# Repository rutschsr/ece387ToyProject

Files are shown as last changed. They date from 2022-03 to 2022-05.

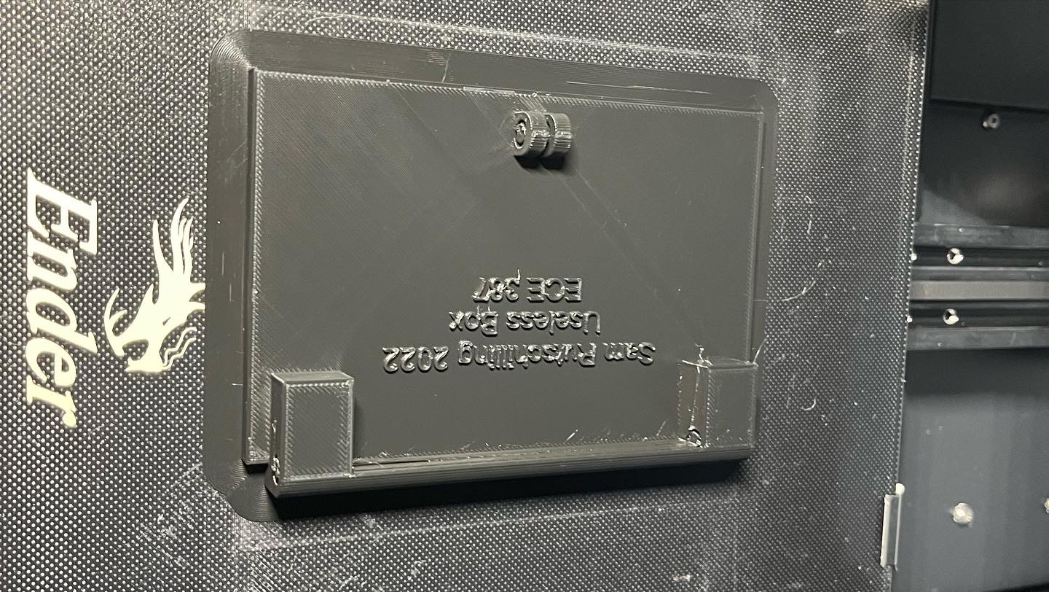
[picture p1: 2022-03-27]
Images/DoorOnPrinter.jpg

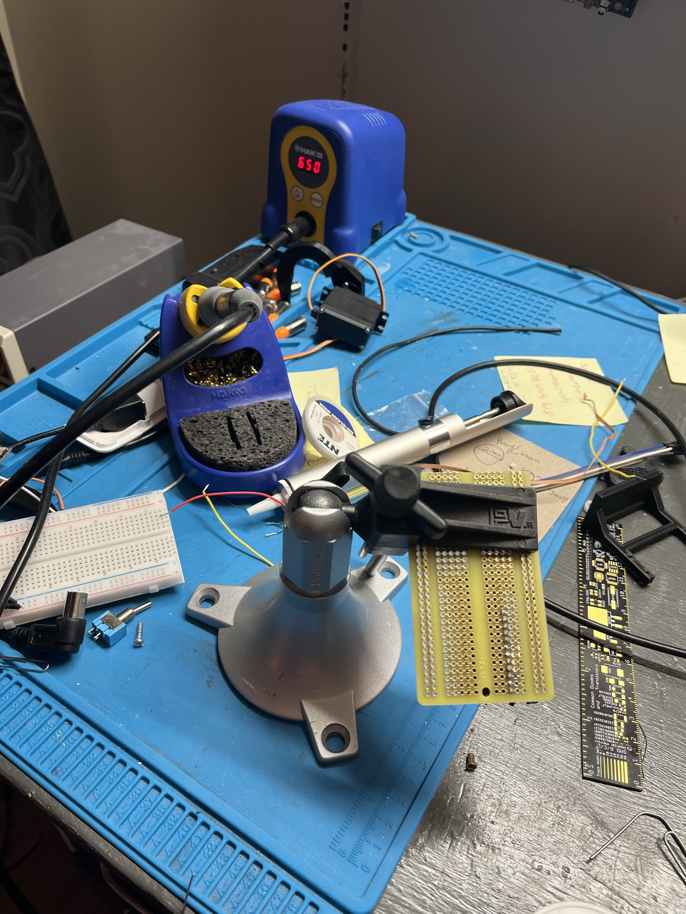
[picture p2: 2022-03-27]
Images/SolderingPerfBoard.JPEG

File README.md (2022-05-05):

# ECE 387 Individual Final Project
## Overview
This useless box is entirely 3D printed and uses a Arduino Micro (ATMEGA 32U) programmed in C using AVR-GCC and AVRDUDE. 

The operation of the Useless Box toy is very simple ... there are two switches, and when each of them are turned on, an arm emerges from inside the box and turns it back off. Therefore the Useless Box serves no real function: it is "useless".

## Operational Demonstration

Img alt text (https://www.youtube.com/watch?v=gphNHizoBe4)

## Operational Overview

The Useless box is a simple toy; it turns the switch off when it is turned on by a user. 

## 3D Printed Parts

I designed all of the mechanical parts for the Useless Box in Autodesk Fusion 360. All of the design files are located in this [Folder](https://github.com/rutschsr/ece387ToyProject/tree/main/3-D%20Parts). Each part was "sliced" (split into layers and 3D printer gcode) using [Utlimaker Cura](https://ultimaker.com/software/ultimaker-cura). I then printed each of the pieces on my Creality Ender 3 V2 3D printer using PLA (polyactic acid) filament. Each piece is is hollow and includes between 40 and 60% fill in a triangular manner to reduce print time and increase strength.

PLA Filament

### Box Bottom

Box in Fusion 360

Box in Autodesk Fusion 360. I exported the drawing to Utilimaker Cura to "slice" it before it was printed.

Box Starting to print

A raspberry pi running Octoprint is connected to my printer which provides a web interface to upload drawings and control the printer from. This printer is connected to the raspberry pi using a micro usb cable.

Complete Bottom of Box on Printer

The bottom of the box used nearly the entire print volume of the printer, took approximately 22 hours to complete, and used approximately 200g ($4-5) of material.

### Box Top

Finished Top

The top of the Useless box, still on the printer. The larger holes are where the switches are mounted, and the smaller holes are screw holes.

### Box Door

Useless box door on printer

The box with hinge mounts on the printer. The raised area on the bottom was originally planned to be a rubber band mount to close the door, but this was not necessary as the door closes by itself.

### Servo Mount

Original Small Servo Mount

The original small servo mount with a servo motor. This motor did not have enough torque and was replaced with a larger motor. The design of the Servo mount stayed the same design but was slightly larger.

### Servo Arm
Brackets and Arms Printing

The brackets and arms also took some trial and error to get correct. The larger servo motors meant that the arms had to be offset to turn off the switches, as the box was not wide enough. This was the only real design change with the arm. I used screws to attach the arm to a mount that came with the servo. This just relies on friction between the gears to stay.

## Assembly

Servo Motors inside Box

Servo Motors mounted inside The Box with switches and offset arms installed. From this view the width of the servo motors and box that required the arms to offset can be seen.

Assembled Box

Assembled box with the door open.

## Wiring and Connections
Useless Box Schematic Diagram
Above is the Schematic Diagram showing the connections for the Useless Box.

My Useless Box accepts a 5-7 V input on either the VIN jack on the outside of the box near the power switch, or the internal battery box which holds four AA batteries.

Internally, the servo motors are powered directly from the VIN port with no voltage regulation and this is why the input is limited to 7 volts. The Arduino Micro is then powered through its VIN pin. On the Arduino two digital input pins are used for the switches, and two PWM pins are used to control the servos. The wiring is very simple, with the only components being the servo motors, the switches, and bleed resistors for the switches.

Soldering perf board in progress

All of the connections are soldered or socketed to improve the reliability. I used a solder perfboard to attach all of the components and header pins for the Arduino and Servo motors.

Arduino Micro on PerfBoard

The Servo headers are on the bottom left of the perfboard, while the black 4 wire cable goes to the switches mounted on the top of the box. After I soldered the components on to the perfboard I used hotglue on all connections to ensure the wires do not break off at their connections.

## Issues

There were several issues and design changes while building the Useless Box. The first was my original choice for servo motor was very small 9g servo motors. After adding a large arm to be able to reach the switch, the motors did not have enough torque to turn the switches off. I than purchased some 20g replacement servos that are much larger and have much more torque. This required other design changes, however. Since the new motors were larger I had to redesign both the servo mounts and the servo arms. The mounts had to sit lower and be longer to fit the larger motor. The Servo arms had to have an offset so the arm would line up with a switch.

Another issue I experienced was with the Arduino. Originally I planned on using an Arduino Uno clone that I had been gifted several years ago. This has the same ATMEGA A328P on the official Arduino Uno, but as is common with the clones, does not have isolation between the USB power supply and board power supply. I found this out the hard way, by having power from my bench power supply applied through the VIN pin and USB power connected for programming. The ATMEGA microcontroller kept functioning but the USB controller failed and lost the ability to communicate. I then switched to a Arduino micro I had sitting around in preperation for a different project which fits much better inside the box but had its own challenges, such as the surface mounted micro USB programming port I managed to tear off the board almost immediately. Thankfully this was easily fixed with some solder and a few minutes of time. The real issue with the Arduino Micro came when it was time to program it in C. Those issues are explained in more detail in the C code section.

The final issue I had was following the input voltage requirements for the Servo motors. Since the servo motors are connected to the VIN connection and voltage is not regulated the voltage must stay within the servo's voltage rating of 4.0-7.2V even though the Arduino is rated for higher voltage. Unfortunately, I did not follow this and connected the Useless box to a 12V power supply I have with the same barrel jack. This did not immediately cause a failure, but one of the servos did eventually fail (and let the smoke out). I replaced the servo with a spare and it has been functioning correctly (at the correct, 5V input) since.

## Arduino Programming

The Arduino (C++) program I used for testing started with the Arduino example code for sweeping the servo motor. It is modified to move the servo motors based on the switch position. The code is located in the [Arduino Folder](https://github.com/rutschsr/ece387ToyProject/tree/main/Arduino/SimpleTest). It uses two counters in the repeating loop part of the program to sweep each of the servos up when the switch was on, and then sweep it down when it was off. This required two for loops as since the servos are sitting opposite each other, they are rotating in the opposite direction. Also included in this code was code to check that the desired position for the Servos was not exceeding what it needed to in order to turn the switches off. This is important because occassionally the arm gets stuck without turning the switch off, especially if the user is being rough with it. If this motor would get stuck it would put a large amount of stress on the mechanical compoenents and servo motors while also having other unexpected behavior. The counter would count until it overflowed, and then the desired Servo position would become very negative, which also is not desired. The Arduino code also just uses the Arduino Servo library and the Servo.write() method to write the desired location to the servo.

## C code

Although not required for this assignment I chose to challenge myself and implement the code in bare metal C code as well. I experienced two main challenges with this; programming the Arduino Micro Atmega A32U from AVRDUDE, since it operates differently then the A328P and implementing PWM on it, since the counters and registers are different then the A328P. The C code is located in the [src folder](https://github.com/rutschsr/ece387ToyProject/tree/main/src). I used the same python script as the labs to compile and program the arduino, although some modifications to the settings for AVR-GCC and avrdude had to be made to accomidate the ATMEGA A32U.

AVRDUDE and A32U

Programming the A32U from AVRDUDE initially proved to be a challenge but I was eventually able to figure out a procedure that was reliable. As with other labs, I started programming using AVRDUDE in an Ubuntu Virtual machine with the Arduino connection passed through from my Windows laptop. This was unreliable because of the procedure for programming, so eventually I decided to program the Arduino solely from a spare laptop I have that runs Ubuntu natively. 

The Arduino Micro's Atmega A32U microcontroller requires a very specific set of steps to be followed. The reset button must be pushed on the board (The Arduino IDE implements this somehow in software, but I was unable to). Then there are 8 seconds to do the remaining steps: The serial port the Arduino is attatched to must be opened at a rate of 1200bps and then immidiatley closed. I accomplished this by using the serial monitor in the Arduino IDE. Then finally the script that compiles and programs the Arduino using avr-gcc and AVRDUDE must be run. This procedure on the native linux machine had a very high success rate.

The second large issue with programming in C was implementing PWM on the A32U in the Arduino Micro. The registers and counters used for PWM on the A32U are different than those used in the Atmega A328P we used in the labs. I first tried to set up PWM the same was using the different counter configuration for the A32U but this proved time consuming and did not work. I was Thankfully able to find help [Online](https://extremeelectronics.co.in/avr-tutorials/servo-motor-control-by-using-avr-atmega32-microcontroller/) where others had implemented PWM on the Atmega A32U.

With those two issues solved, the rest of the C code is essentially ported from the Arduino Code version. The only differences are syntax and the obvious lack of the Servo.write() method. The C-Code version of the code is what is used for the demonstration video.

## Power Reduction Techniques:
As this project can be battery powered, power reduction techniques are necessary to ensure a long battery life. The useless box can be powered by 4AA batteries in a battery case that is under the useless box door. The box's ATMEGA A32U microcontroller - integrated into the Arduino Micro, is programmed using baremetal C in order to reduce the overhead and power consumption. This also uses direct manipulation of counters for PWM control so any overhead required by the Arduino libraries was eliminated. The battery life is still quite poor however, as the Servo motors can draw approximately 1 amp each under load. When operating under battery power, the AA batteries cannot output 2A for a long period of time, so battery life is poor.

## Improvements:
As with any project, by the time it was finished there were several things that I would do differently if I were to do the project again. One of these changes would be further improving the power consumption. Even with the power reduction techniques described above the power consumption and battery life are still rather poor. One easy power reduction technique I would employ if starting again is controlling the power to the servo motors using a MOSFET, so they would only have power when they are active and have a reason to be moving. Another power reduction technique I would have employed is using interrupts for the switch control, so the microcontroller could be in a ultra low power state when niether of the servos are moving. Finally instead of using the Arduino micro with the ATMEGA 32U microcontroller, I likely would use a bare ATMEGA A328P for the better packaging and power consumption.

Other power improvments for the box could include a rechargable battery system. A rechargable lithium battery could be implemented into the system power it for longer periods of time. This also could be implemented with a USB power source to easier find a power source versus the DC barrel jack on the current Useless Box. As a sidenote, the barrel jack is necessary without a permanant onboard battery due to the high power requirements of the servos that a USB power supply (especially a computer) cannot support.

Mechanical improvements I would make if I were starting again would be to design the bottom of the box with the servo mounts intergrated. This would increase the servo mounts structual integrity, would reduce their movement, and remove the need for the hot glue I added to keep the motors from moving. I also would use screws to mount the servo "arms" to the servo motors instead of relying on friction of the gears to work. While designing the initial bottom of the box I should have also considered the motion of the door opening so that I would not have had to knotch the door on the sides to let it open. This was the first project I had completed with 3-D printed parts and Fusion 360, so it was a learning expierence both with the 3-D design software and my 3-D printer.

## Cost

Cost breakdown. Costs for 3D printed parts are estimated from the slicer's estimate of the filament required for printing.

| Part | Quantity | Cost | Note |
| --- | --- | --- | --- |
| Box Bottom | 1 | $5.74 | PLA |
| Box Top | 1 | $1.10 | PLA |
| Box Door | 1 | $1.02 | PLA |
| Servo Arms | 2 | $0.55 | PLA |
| Servo Mounts | 2 | $0.55 | PLA |
| Original Servos| 2 | $10.99 |  |
| Larger Servos| 2 | $22.35 |  |
| Switches | 2 | $1.60 |  |
| Arduino Micro | 1 | $21.00 |  |
| Perfboard | 1 | $6.99 | Adafruit |
| Hinge Rod | 1 | $8.51 |  |
| Miscelaneous | N/A | $5 | Other Various Parts |

Total: $85.40

## More Information:

Additional Documentation found at: https://srutschilling.net/ECE387/ToyProject/

(Site will be undergoing maintenance between May 15-June 1 2022)

Additional help with PWM on ATMEGA 32U from: https://extremeelectronics.co.in/avr-tutorials/servo-motor-control-by-using-avr-atmega32-microcontroller/

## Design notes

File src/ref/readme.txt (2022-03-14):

Sam Rutschilling
Lab 3: 
ECE 387 Spring 2022
Miami University

Febuary 10,2022

Youtube Demonstration of working project:
https://youtu.be/_FFq0tg9W6I

The Arduino was programmed using modified compile_script on Linux Virtual Machine (slight changes
to change \ to / and remove .exe in avrdude. The script will likely not work completley correctly for Windows machines.

The Com port passed to my Linux Virtual Machine by VMWARE Workstation is defined as /dev/ttyACM0, this is used for programming.
This was also used using the USART library for serial communication while trying to debug.

running the command "python compile_script.py 4" compiles the program and uploads it to the arduino using /dev/ttyACM0.

Additional files and compiled files can be removed then using the command "python compile_script.py 0" This is equivalent to "clean" in Visual Studio.

Also added to the program were Design by contract Pre and Post proccessor functions. The preprocessor functions for the stoplight function were tested in a video linked below.
For this video one of the function calls explicitly calls for two of the lights to be on, this causes the pin 13 led to light up and the program to be in a DBC error state. This
DBC pre function uses Exculsive OR call. PRE and POST DBC functions turn on PIN13 (the built in Arduino LED) if they fail. This tells the user/programmer that an error occured. POST_ errors turn
the LED on for half of the time that PRE_ issues do so that differentiates which function failed. This is helpful for debugging. The compiled program will be smaller and will execute faster without DBC functions
Included. Since they are handled using preprocessor directives it should make no difference to fully remove them as the preprocessor and compiler will ignore them and not compile them if they are turned off. Similarly,
in C++ I have used #If 0 preprocessor directives to turn off complete blocks of code, since they are turned off by preprocessor directives they will be ignored at the preprocessing stage and not handled by the compiler.

Link of DBC Error Video:
https://youtu.be/MKCNsZm0w2o

A Pull down resistor (large value 4K+ Ohm) is necessary for an input button on the arduino. This keeps the input pin grounded and from "floating" if the button is not pushed and the value is not high. This will keep
unexpected results from occuring where the arduino reads the input as high when the button was not pushed.

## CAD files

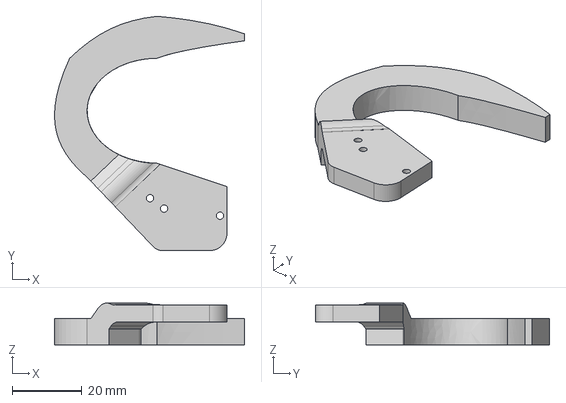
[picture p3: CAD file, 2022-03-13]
3-D Parts/STEP/UselessBoxArmOffset v3.step
54.3 x 67.0 x 12.0 mm

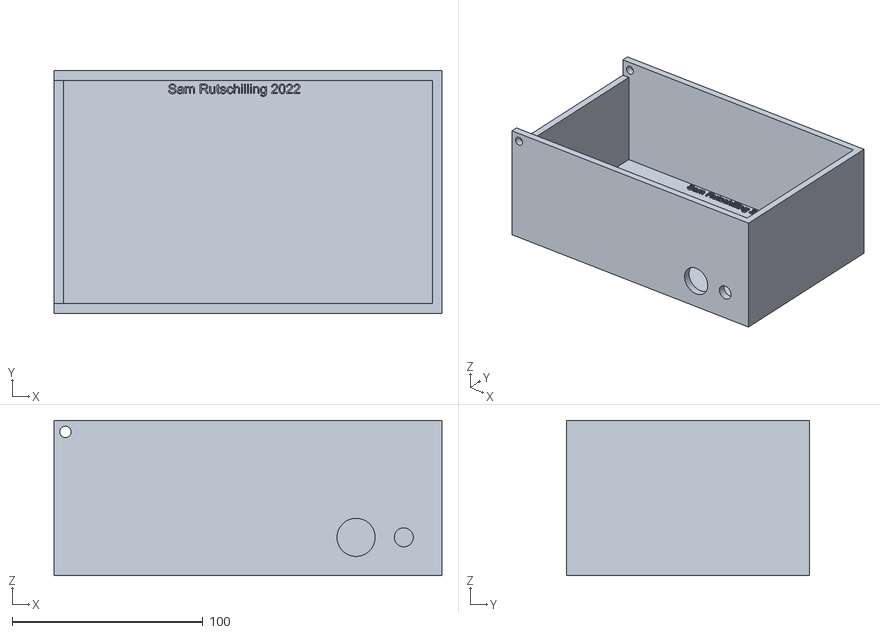
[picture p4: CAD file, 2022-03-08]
3-D Parts/STL/UselessBoxBottom v3.stl
203.2 x 127.0 x 81.2

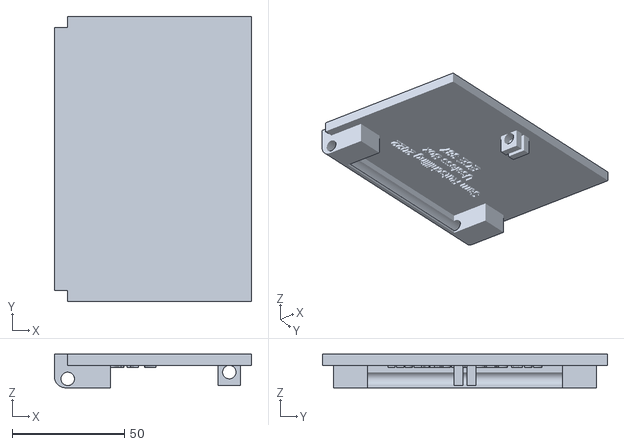
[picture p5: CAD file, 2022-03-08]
3-D Parts/STL/UselessBoxDoor v3.stl
88.0 x 127.0 x 15.0

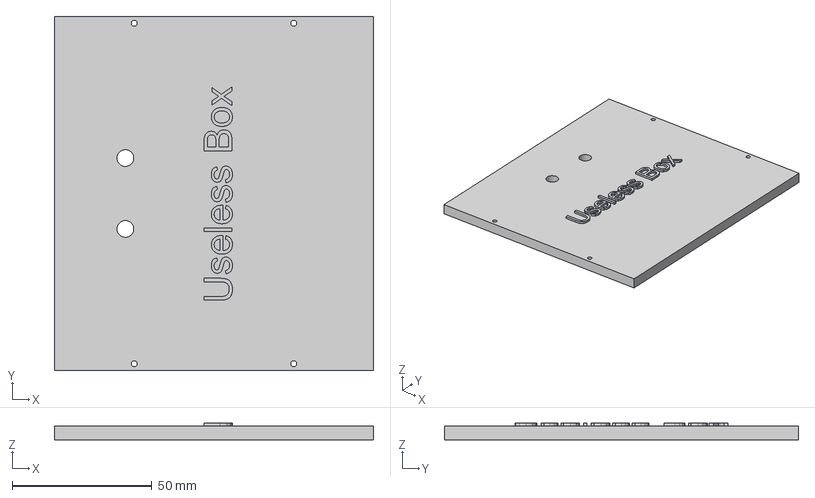
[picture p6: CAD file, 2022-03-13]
3-D Parts/STEP/UselessBoxTop v6.step
114.3 x 127.0 x 6.00 mm

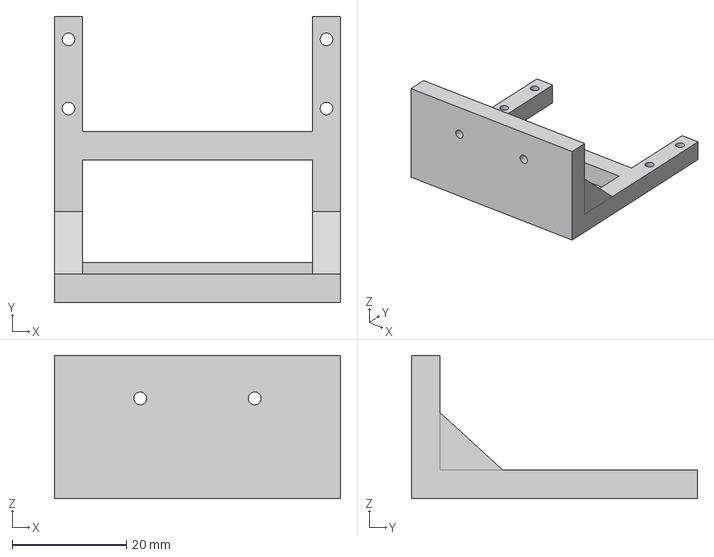
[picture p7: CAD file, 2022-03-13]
3-D Parts/STEP/UselessBoxServoMountBiggerServo v1.step
50.0 x 50.0 x 25.0 mm

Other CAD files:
3-D Parts/STEP/UselessBoxBottom v4.step
3-D Parts/STL/UselessBoxTop v5.stl
3-D Parts/STEP/UselessBoxArmOffsetReflect v2.step
3-D Parts/STEP/UselessBoxDoor v4.step
3-D Parts/Fusion 360/UselessBoxArmOffset v3.f3d
3-D Parts/Fusion 360/UselessBoxArmOffsetReflect v2.f3d
3-D Parts/Fusion 360/UselessBoxBottom v3.f3d
3-D Parts/Fusion 360/UselessBoxDoor v4.f3d
3-D Parts/Fusion 360/UselessBoxServoMountBiggerServo v1.f3d
3-D Parts/Fusion 360/UselessBoxTop v6.f3d

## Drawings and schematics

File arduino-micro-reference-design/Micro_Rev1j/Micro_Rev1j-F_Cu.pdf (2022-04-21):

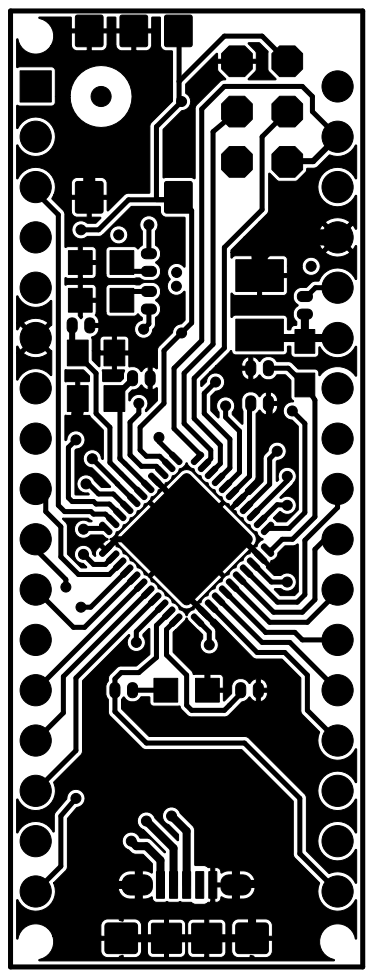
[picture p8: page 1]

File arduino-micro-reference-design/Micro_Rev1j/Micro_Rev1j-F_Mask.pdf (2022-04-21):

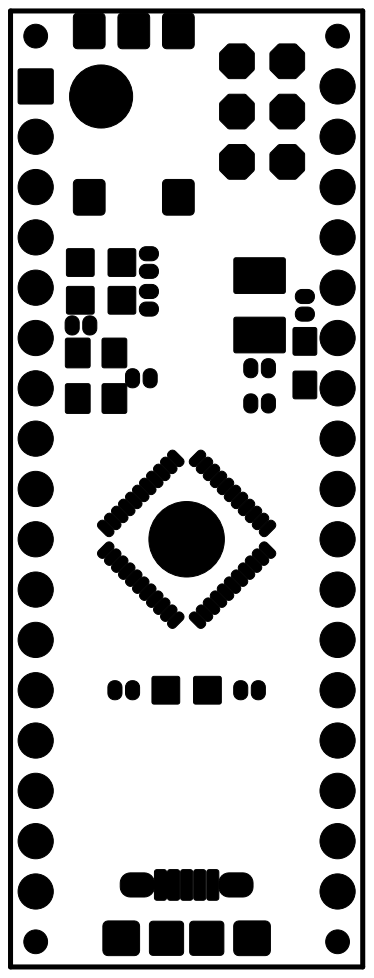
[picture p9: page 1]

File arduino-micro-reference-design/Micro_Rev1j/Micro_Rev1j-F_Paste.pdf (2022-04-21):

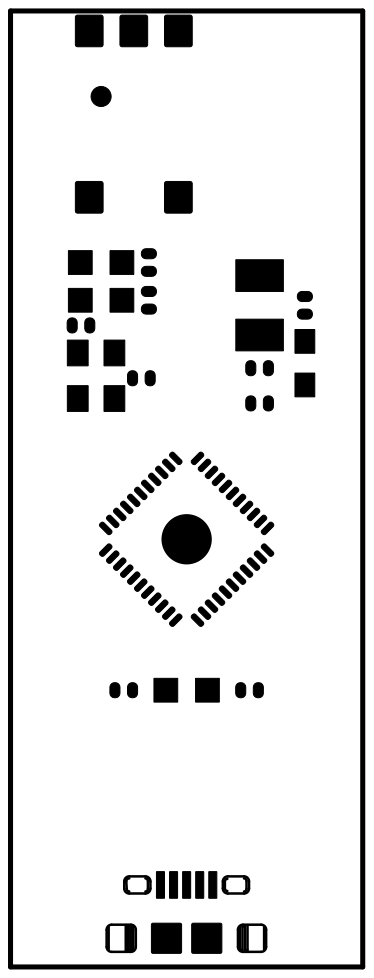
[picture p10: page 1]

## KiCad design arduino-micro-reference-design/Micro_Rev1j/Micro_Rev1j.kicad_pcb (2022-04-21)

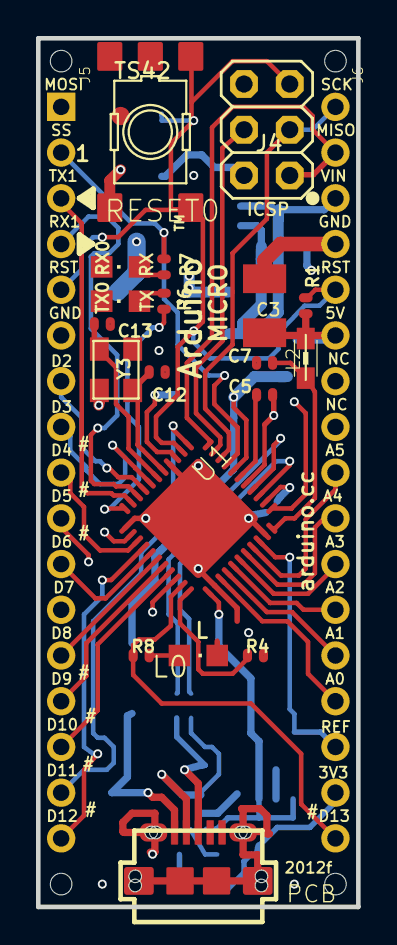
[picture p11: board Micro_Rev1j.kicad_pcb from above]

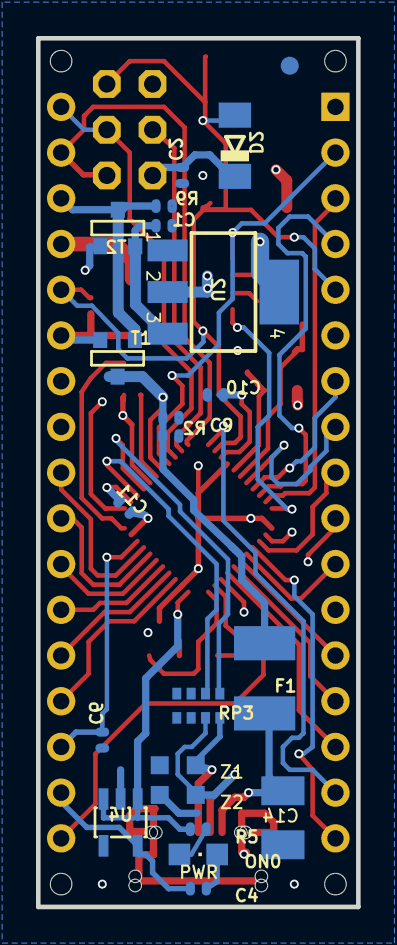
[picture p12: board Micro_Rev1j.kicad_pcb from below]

Board: 4 copper layers, 17.8 x 48.3 mm, 49 parts (22 on the bottom side), 47 nets.

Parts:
@HOLE0, @HOLE1, @HOLE2, @HOLE3: (no value)
C1, C2, C6, C9, C10, C11: 100n; C0402
C3, C14: 22u; SMC_B
C4, C5, C7: 1uF; C0402
C12, C13: 22pF; C0402
D2: CD1206-S01575; MINIMELF
F1: MF-MSMF050-2 500mA; L1812
FRAME1: DNP; FRAME
J3: USB-MICRO!!!; CON2_USB_MICRO_B_AT
J4: 3x2M; 2X03
J5: HEAD17-NOSS
J6: HEAD17-NOSS-1
L0: green; CHIPLED_0805
L2: MH2029-300Y; 0805
ON0: blue; CHIPLED_0805
R1, R2, R4, R9: 10K; R0402
R5, R6, R7, R8: 1K; R0402
RESET0: TS42
RP3: 22R; CAY16
RX0: yellow; CHIPLED_0805
T1: FDN340P/PMV48XP; SOT-23
T2: PMV48XP; SOT-23
TX0: yellow; CHIPLED_0805
U1: ATMEGA32U4-XUMU; QFN44ML7X7
U2: NCP1117-5; SOT223
U4: LP2985-33DBVR; SOT23-DBV
U$37: FIDUCIALMOUNT; FIDUCIA-MOUNT
U$53: FIDUCIAL1X2; FIDUCIAL-1X2
Y3: 16MHz KX-7; CRYSTAL-3.2-2.5
Z1, Z2: CG0603MLC-05E; CT_CN0603

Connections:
3V3: C4.1, J6.16, U4.5
+5V: C2.1, C3.+, C10.1, C11.1, D2.C, J4.2, J6.6, L2.1, R1.1, R5.1, T1.2, T2.3, U1.2, U1.14, U1.24, U1.34, U2.2, U2.4, U4.1, U4.3
+VIN: C1.1, T2.2, U2.3
A0: J6.14, U1.36
A1: J6.13, U1.37
A2: J6.12, U1.38
A3: J6.11, U1.39
A4: J6.10, U1.40
A5: J6.9, U1.41
AREF: C6.1, J6.15, U1.42
AVCC: C7.1, L2.2, U1.44
D0/RX: J5.4, U1.20
D1/TX: J5.3, U1.21
D2/SDA: J5.7, U1.19
D3/SCL: J5.8, U1.18
D4*: J5.9, U1.25
D5*: J5.10, U1.31
D6*: J5.11, U1.27
D7: J5.12, U1.1
D+: J3.P3, RP3.8, Z1.1
D-: J3.P2, RP3.7, Z2.1
GND: C1.2, C2.2, C3.-, C4.2, C5.2, C6.2, C7.2, C9.2, C10.2, C11.2, C12.1, C13.1, C14.-, J3.P5, J3.S1, J3.S2, J3.S3, J3.S4, J3.S5, J3.S6, J4.6, J5.6, J6.4, L0.C, ON0.C, R2.1, R4.2, R9.1, RESET0.3, RESET0.4, RESET0.5, RP3.3, RP3.4, RP3.5, RP3.6, RX0.C, TX0.C, U1.5, U1.15, U1.23, U1.35, U1.43, U1.EXP, U2.1, U4.2, Y3.2, Y3.4, Z1.2, Z2.2
HWB: R4.1, U1.33
IO8: J5.13, U1.28
IO9*: J5.14, U1.29
IO10*: J5.15, U1.30
IO11*: J5.16, U1.12
IO12*: J5.17, U1.26
IO13*: J6.17, R8.1, U1.32
MISO: J4.1, J6.2, U1.11
MOSI: J4.4, J5.1, U1.10
unnamed: R7.2, RX0.A
unnamed: ON0.A, R5.2
unnamed: R6.2, TX0.A
unnamed: L0.A, R8.2
RD+: RP3.1, U1.4
RD-: RP3.2, U1.3
RESET: D2.A, J4.5, J5.5, J6.5, R1.2, RESET0.1, RESET0.2, U1.13
RXLED/SS: J5.2, R7.1, U1.8
SCK: J4.3, J6.1, U1.9
TXLED: R6.1, U1.22
UCAP: C5.1, U1.6
VIN: J6.3, R9.2, T1.3, T2.1
VUSB: C9.1, F1.2, R2.2, T1.1, U1.7
VUSBD: C14.+, F1.1, J3.P1
XTAL1: C13.2, U1.17, Y3.3
XTAL2: C12.2, U1.16, Y3.1

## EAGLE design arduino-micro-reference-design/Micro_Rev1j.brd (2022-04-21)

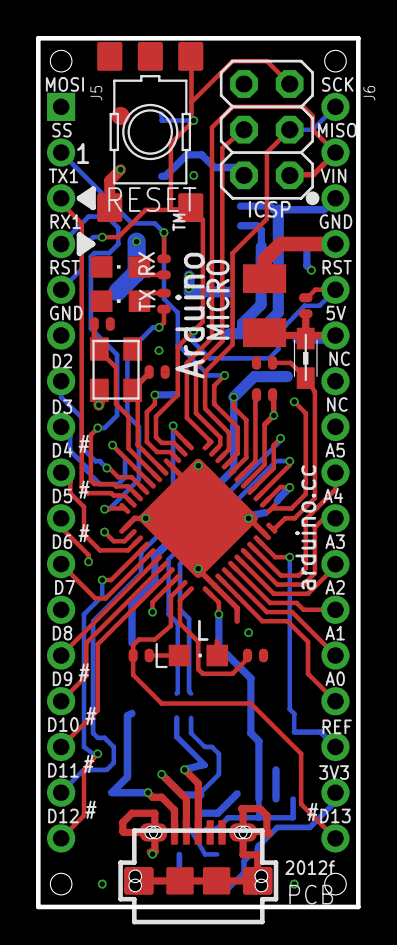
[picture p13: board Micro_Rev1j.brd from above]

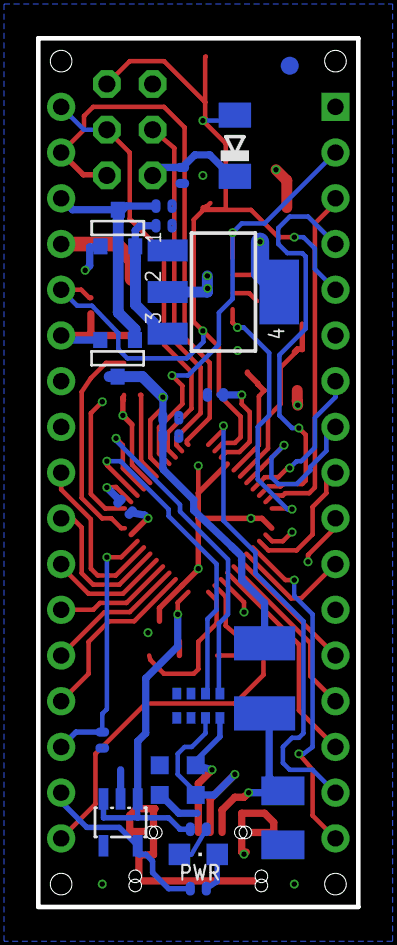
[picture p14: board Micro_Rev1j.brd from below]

Board: 4 copper layers, 17.8 x 48.3 mm, 45 parts (22 on the bottom side), 47 nets.

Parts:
C1, C2, C6, C9, C10, C11: 100n; C0402
C3, C14: 22u; SMC_B
C4, C5, C7: 1uF; C0402
C12, C13: 22pF; C0402
D2: CD1206-S01575; MINIMELF
F1: MF-MSMF050-2 500mA; L1812
FRAME1: DNP; FRAME
J3: USB-MICRO!!!; CON2_USB_MICRO_B_AT
J4: 3x2M; 2X03
J5: HEAD17-NOSS
J6: HEAD17-NOSS-1
L: green; CHIPLED_0805
L2: MH2029-300Y; 0805
ON: blue; CHIPLED_0805
R1, R2, R4, R9: 10K; R0402
R5, R6, R7, R8: 1K; R0402
RESET: TS42
RP3: 22R; CAY16
RX: yellow; CHIPLED_0805
T1: FDN340P/PMV48XP; SOT-23
T2: PMV48XP; SOT-23
TX: yellow; CHIPLED_0805
U1: ATMEGA32U4-XUMU; QFN44ML7X7
U2: NCP1117-5; SOT223
U4: LP2985-33DBVR; SOT23-DBV
U$37: FIDUCIALMOUNT; FIDUCIA-MOUNT
U$53: FIDUCIAL1X2; FIDUCIAL-1X2
Y3: 16MHz KX-7; CRYSTAL-3.2-2.5
Z1, Z2: CG0603MLC-05E; CT/CN0603

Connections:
3V3: C4.1, J6.16, U4.5
+5V: C2.1, C3.+, C10.1, C11.1, D2.C, J4.2, J6.6, L2.1, R1.1, R5.1, T1.2, T2.3, U1.2, U1.14, U1.24, U1.34, U2.2, U2.4, U4.1, U4.3
+VIN: C1.1, T2.2, U2.3
A0: J6.14, U1.36
A1: J6.13, U1.37
A2: J6.12, U1.38
A3: J6.11, U1.39
A4: J6.10, U1.40
A5: J6.9, U1.41
AREF: C6.1, J6.15, U1.42
AVCC: C7.1, L2.2, U1.44
D0/RX: J5.4, U1.20
D1/TX: J5.3, U1.21
D2/SDA: J5.7, U1.19
D3/SCL: J5.8, U1.18
D4*: J5.9, U1.25
D5*: J5.10, U1.31
D6*: J5.11, U1.27
D7: J5.12, U1.1
D+: J3.P3, RP3.8, Z1.1
D-: J3.P2, RP3.7, Z2.1
GND: C1.2, C2.2, C3.-, C4.2, C5.2, C6.2, C7.2, C9.2, C10.2, C11.2, C12.1, C13.1, C14.-, J3.P5, J3.S1, J3.S2, J3.S3, J3.S4, J3.S5, J3.S6, J4.6, J5.6, J6.4, L.C, ON.C, R2.1, R4.2, R9.1, RESET.3, RESET.4, RESET.5, RP3.3, RP3.4, RP3.5, RP3.6, RX.C, TX.C, U1.5, U1.15, U1.23, U1.35, U1.43, U1.EXP, U2.1, U4.2, Y3.2, Y3.4, Z1.2, Z2.2
HWB: R4.1, U1.33
IO8: J5.13, U1.28
IO9*: J5.14, U1.29
IO10*: J5.15, U1.30
IO11*: J5.16, U1.12
IO12*: J5.17, U1.26
IO13*: J6.17, R8.1, U1.32
MISO: J4.1, J6.2, U1.11
MOSI: J4.4, J5.1, U1.10
unnamed: R7.2, RX.A
unnamed: ON.A, R5.2
unnamed: R6.2, TX.A
unnamed: L.A, R8.2
RD+: RP3.1, U1.4
RD-: RP3.2, U1.3
RESET: D2.A, J4.5, J5.5, J6.5, R1.2, RESET.1, RESET.2, U1.13
RXLED/SS: J5.2, R7.1, U1.8
SCK: J4.3, J6.1, U1.9
TXLED: R6.1, U1.22
UCAP: C5.1, U1.6
VIN: J6.3, R9.2, T1.3, T2.1
VUSB: C9.1, F1.2, R2.2, T1.1, U1.7
VUSBD: C14.+, F1.1, J3.P1
XTAL1: C13.2, U1.17, Y3.3
XTAL2: C12.2, U1.16, Y3.1

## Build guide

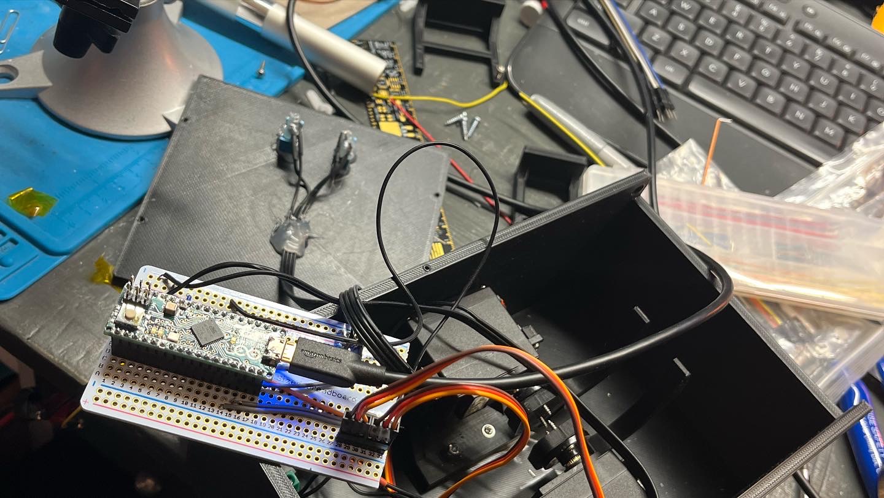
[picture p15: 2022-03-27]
Images/WiringConnected.jpg

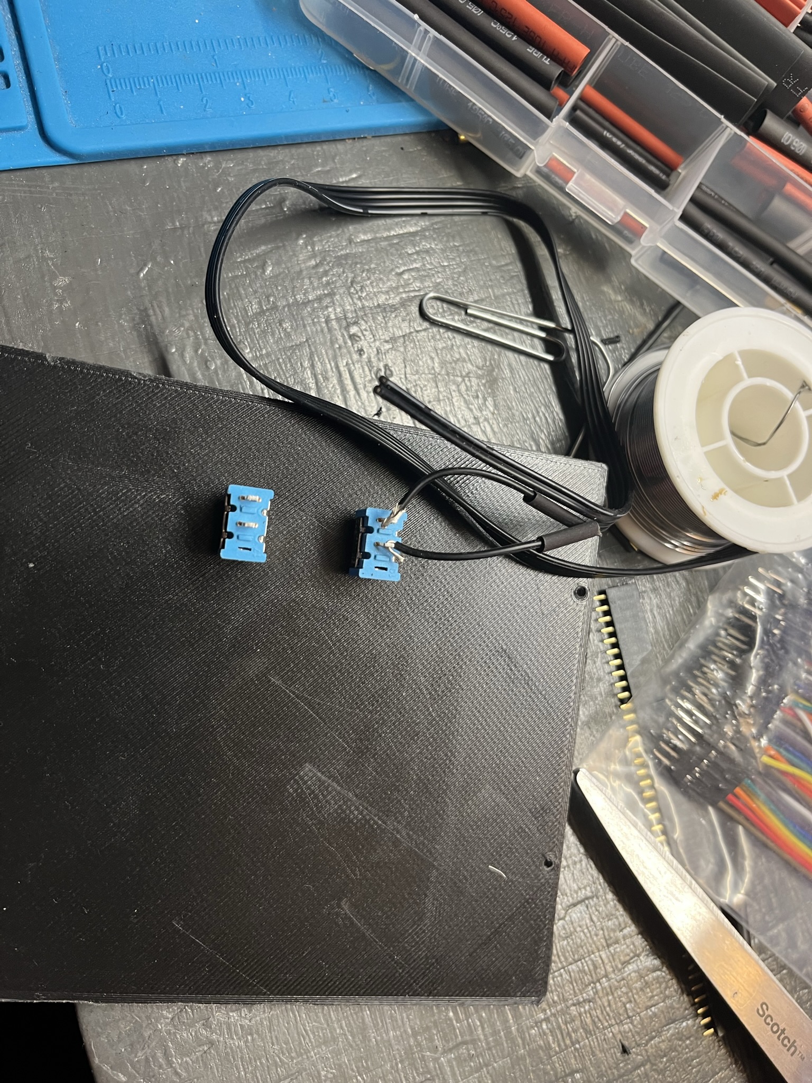
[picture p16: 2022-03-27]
Images/SolderingSwitches.JPEG

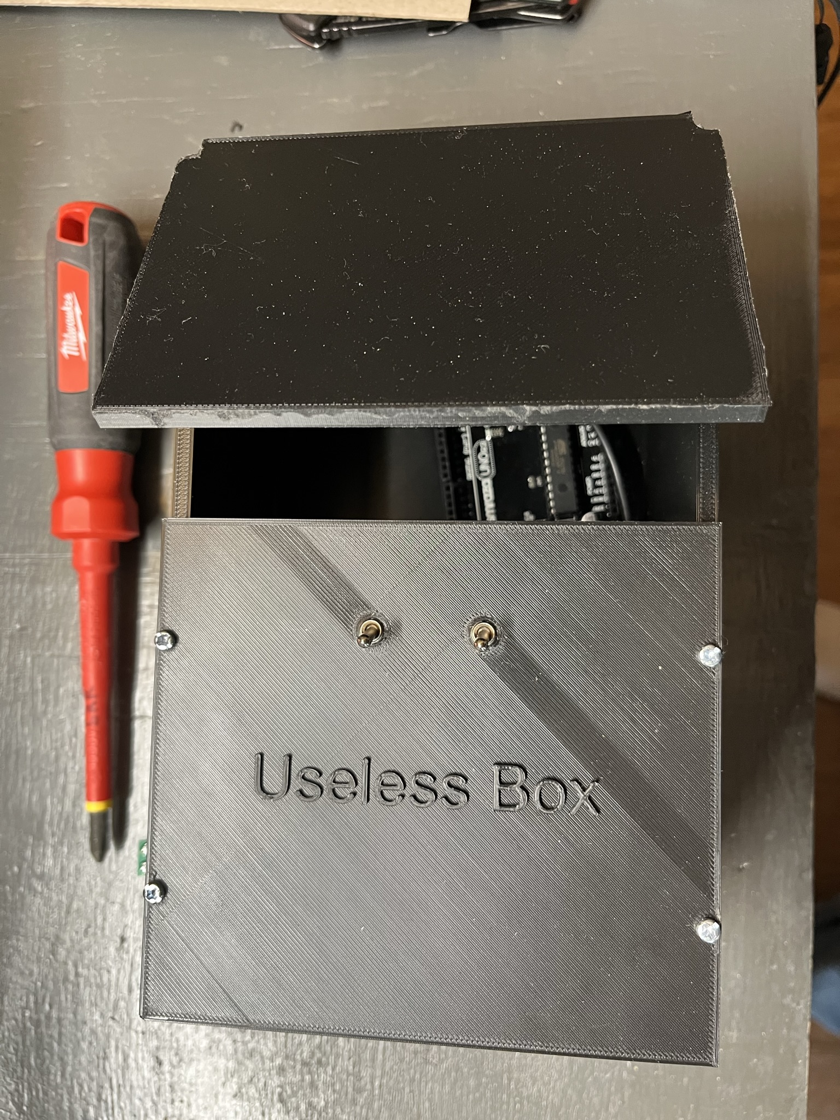
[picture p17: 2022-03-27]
Images/AssembledBox1.JPEG

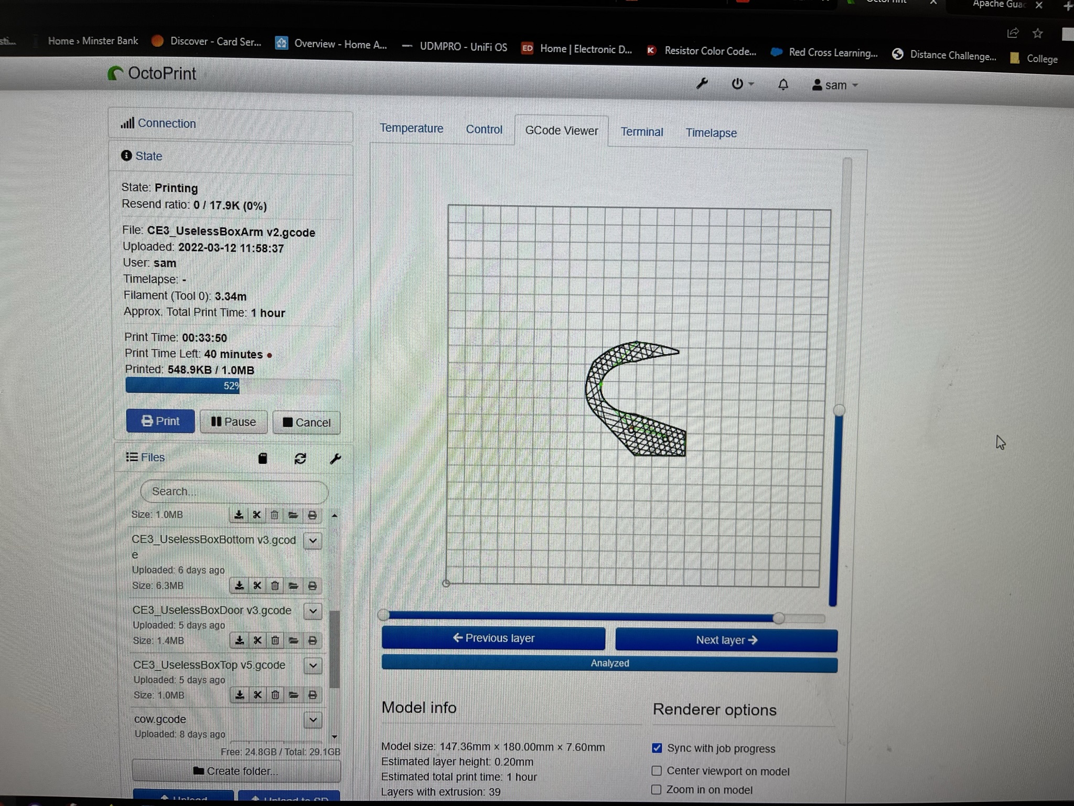
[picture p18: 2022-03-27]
Images/ArmInOctoPrint.JPEG

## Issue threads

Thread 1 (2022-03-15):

Create C code

rutschsr, 2022-03-15:
Create C code with notes in Arduino code. Should use hardware PWM as in stoplight lab. Inputs do not need debouncing as they are switches not buttons.

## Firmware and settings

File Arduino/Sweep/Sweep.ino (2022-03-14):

/* Sweep
 by BARRAGAN <http://barraganstudio.com>
 This example code is in the public domain.

 modified 8 Nov 2013
 by Scott Fitzgerald
 http://www.arduino.cc/en/Tutorial/Sweep
*/

#include <Servo.h>

Servo myservo;  // create servo object to control a servo
// twelve servo objects can be created on most boards
Servo Servo2;

int pos = 0;    // variable to store the servo position

void setup() {
  myservo.attach(9);
  Servo2.attach(10);// attaches the servo on pin 9 to the servo object
}

void loop() {
  for (pos = 50; pos <= 138; pos += 1) { // goes from 0 degrees to 180 degrees
    // in steps of 1 degree
    myservo.write(pos);
    Servo2.write(175-pos); // tell servo to go to position in variable 'pos'
    delay(5);                       // waits 15ms for the servo to reach the position
  }
    myservo.write(138);
    Servo2.write(175-138);// tell servo to go to position in variable 'pos'
    delay(1000); 
  
  for (pos = 138; pos >= 50; pos -= 1) { // goes from 180 degrees to 0 degrees
    myservo.write(pos);
    Servo2.write(175-pos);              // tell servo to go to position in variable 'pos'
    delay(5);                       // waits 15ms for the servo to reach the position
  }
  myservo.write(50);
  Servo2.write(175-50);
  // tell servo to go to position in variable 'pos'
    delay(5000); 
}

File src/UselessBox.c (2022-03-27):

#include <avr/io.h>
#include <util/delay.h>

//PWM on Atmega32u using help from:
//https://extremeelectronics.co.in/avr-tutorials/servo-motor-control-by-using-avr-atmega32-microcontroller/

// Switch 1 on 6 (PD7)
// Switch 2 on 7 (PE6)
#define button1 PD7
#define button2 PE6

// Servo 1 on 9 (PB5)
// Servo 2 on 10 (PB6)

// Forward Declerations
void pwm_hw_setup();
void pwm(int servo1, int servo2);

int button1state = 1;
int button2state = 1;
int servo1pos = 85;
int servo2pos = 125;

int main()
{
     pwm_hw_setup();

    DDRC |= _BV(DDC7);

    while (1)
    {
        button1state = (PIND & (1 << button1));
        button2state = (PINE & (1 << button2));

       if(button1state==0){
           if(servo1pos<200){
               servo1pos++;
           }
       }
       else{
           if(servo1pos>=85){
               servo1pos--;
           }
       }
       
       
       
        if (button2state==0)
        {
            PORTC |= _BV(PORTC7);
            if(servo2pos>60){
                servo2pos--;
            }
        }
        else
        {
            if(servo2pos<=185){
                servo2pos++;
            }
            PORTC &= ~_BV(PORTC7);
        }
        pwm(servo1pos ,servo2pos);
        _delay_ms(2);
    }
}

void pwm_hw_setup()
{
	TCCR1A|=(1<<COM1A1)|(1<<COM1B1)|(1<<WGM11);        //NON Inverted PWM
   TCCR1B|=(1<<WGM13)|(1<<WGM12)|(1<<CS11)|(1<<CS10); //PRESCALER=64 MODE 14(FAST PWM)

   ICR1=4999;  //fPWM=50Hz (Period = 20ms Standard).

   DDRB|=(1<<PB5)|(1<<PB6);   //PWM Pins as Out
}


void pwm(int servo1, int servo2)
{
	servo1=servo1*2+100;
    servo2=servo2*2+100;

	
      OCR1A=servo1;  //90 degree
      OCR1B=servo2;  //90 degree



	
	
		/* IF - button1 is pressed - increase the PWM duty cycle by 12.5% or 1/8 */
		// PIN 10 - yellow
		//OCR1A=(float)servo1/(float)180*step16;
		// PIN 11 - green
		//OCR1B =(float)servo2/(float)180*step16;
		// PIN 3 - red
		//OCR2B += step8;
	
}

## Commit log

2022-03-08 Add STL
    add STL files for some of the 3D printed parts
    [UselessBoxBottom v3.stl, UselessBoxDoor v3.stl, UselessBoxTop v5.stl]
2022-03-13 Add Remaining 3-D print files
    [UselessBoxArmOffset v3.f3d, UselessBoxArmOffset v3.step, UselessBoxArmOffsetReflect v2.f3d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]
2022-03-15 Update SimpleTest.ino
    Add some new behavior to fix errors with counters running too high
    [SimpleTest.ino]
2022-03-27 Switch Test
2022-03-27 Switch Testing
2022-03-27 PWM work
2022-03-27 PWM working
2022-04-21 Add some arduino micro PCB files
    [Micro_Rev1j.brd, Micro_Rev1j.kicad_pcb, Micro_Rev1j.sch]

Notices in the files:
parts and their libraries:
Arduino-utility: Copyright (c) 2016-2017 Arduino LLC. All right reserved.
